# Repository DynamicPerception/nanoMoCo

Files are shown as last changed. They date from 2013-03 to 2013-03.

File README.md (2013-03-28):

nanoMoCo Stepper Controller/Driver
==================================

The nanoMoCo stepper driver/controller is a specialized, Arduino-compatible* device specifically designed to enable advanced multi-axis stepper-based robotics and automation projects less expensive, and easier to create.

This github contains the Eagle files, BOM, and Sketchup files for this board.  To purchase a pre-made board, see http://dynamicperception.com/products/nanomoco-stepper-drivercontroller

Key features of the nanoMoCo include:

- Atmega328P processor running at 16MHz
- 8-16V DC Operation
- Integrated A4983/A4988 bi-polar chopping driver with up to 16x microstepping
     - Up to 800 mA/coil without active cooling
     - Up to 1.5 A/coil with active cooling
- Dual opto-coupled outputs for safe interaction with other devices
- Integrated RS485 bus for multi-node communication over long distances with only two wires
- Leverage the OpenMoCo AVR Libraries and OpenMoCo Qt Libraries to create new software and applications

* requires a special USB to RS485 adapter to use with the Arduino IDE

See http://dynamicperception.com/docs/nanomoco for more information

License and Copyright
---------------------

nanoMoCo is Copyright (c) 2012-2013 Dynamic Perception LLC.

All files shared under the Creative Commons Attibution-Share-Alike 3.0 License.

The nanoMoCo name is a trademark of Dynamic Perception LLC.

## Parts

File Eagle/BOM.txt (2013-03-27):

Part	Value		Device			Sheet	Part #

C1	0.1uF		CAP0402			1	GRM155R71A104KA01D

C10	0.1uF		CAP0402			1	GRM155R71A104KA01D

C2	0.1uF		C-EUC1608		1	CGA3E2X7R1H104K

C3	0.1uF		C-EUC1608		1	CGA3E2X7R1H104K

C4	0.1uF		C-EUC1608		1	CGA3E2X7R1H104K

C7	0.1uF		C-EUC1608		1	CGA3E2X7R1H104K

C5	6pF		CAP0402			1	GRM1555C1H6R0DZ01D

C8	6pF		CAP0402			1	GRM1555C1H6R0DZ01D
C6	0.22uF		C-EUC0805		1	C0805C224K5RACTU

C13	10uF		CAP_POL1206		1	T491A106M020AT

C19	10uF		CAP_POL1206		1	T491A106M020AT

IC1	SN75176A	SN65176D		1	SN75176AD

IC2	A4983		A4983			1	A4983SETTR-T

JP1	COMM		PINHD-2X7		1	not placed

JP2	MOTOR		PINHD-1X4		1	not placed

JP3	ICSP		PINHD-2X3		1	not placed
JP4	ISO		PINHD-1X4		1	not placed

SER	SER		PINHD-2X2		1	not placed

OK1	ACPL-227	ACPL-227		1	ILD207T

OUT1	LED		LEDCHIPLED_0603		1	SML-P12VTT86

PWR	LED		LEDCHIPLED_0603		1	SML-P12VTT86

R1	100K		RESISTOR0402		1	not placed

R8	100K		RESISTOR0402		1	not placed

R2	5.1k		RESISTOR0402		1	RC0402FR-075K1L

R3	5.1k		RESISTOR0402		1	RC0402FR-075K1L

R15	5.1k		RESISTOR0402		1	RC0402FR-075K1L

R4	2.49k		RESISTOR0402		1	RR0510P-2491-D

R5	62		RESISTOR0402		1	CRCW040262R0FKED

R6	10K		RESISTOR0402		1	CRCW040210K0FKEDHP

R7	41.2		RESISTOR0402		1	CRCW040241R2FKED

R9	100		RESISTOR0402		1	not placed

R10	0.01		R-US_R0603		1	ERJ-M03NF10MV

R12	0.01		R-US_R0603		1	ERJ-M03NF10MV

R13	20k		RESISTOR0402		1	ERA-2AEB203X

R14	470		RESISTOR0402		1	RK73B1ETTP471J

R16	470		RESISTOR0402		1	RK73B1ETTP471J

T2	CMPT2369	BCW60-NPN-SOT23-BEC	1	CMPT2369

U$1	CADJ		TC33X-2			1	TC33X-2-103E

U$3	3.2X2.5MMCRYSTAL 3.2X2.5MMCRYSTAL	1	CX3225SB16000D0FLJZZ

U1	ATMEGA328	ATMEGA168		1	ATMEGA328P-AU

U2	MIC5205-5.0YM5	V_REG_LDOSMD		1	MIC5205-5.0YM5 TR

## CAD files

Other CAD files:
Sketchup/nmoco-brd-1t1.skp
Sketchup/nmoco-brd.skp

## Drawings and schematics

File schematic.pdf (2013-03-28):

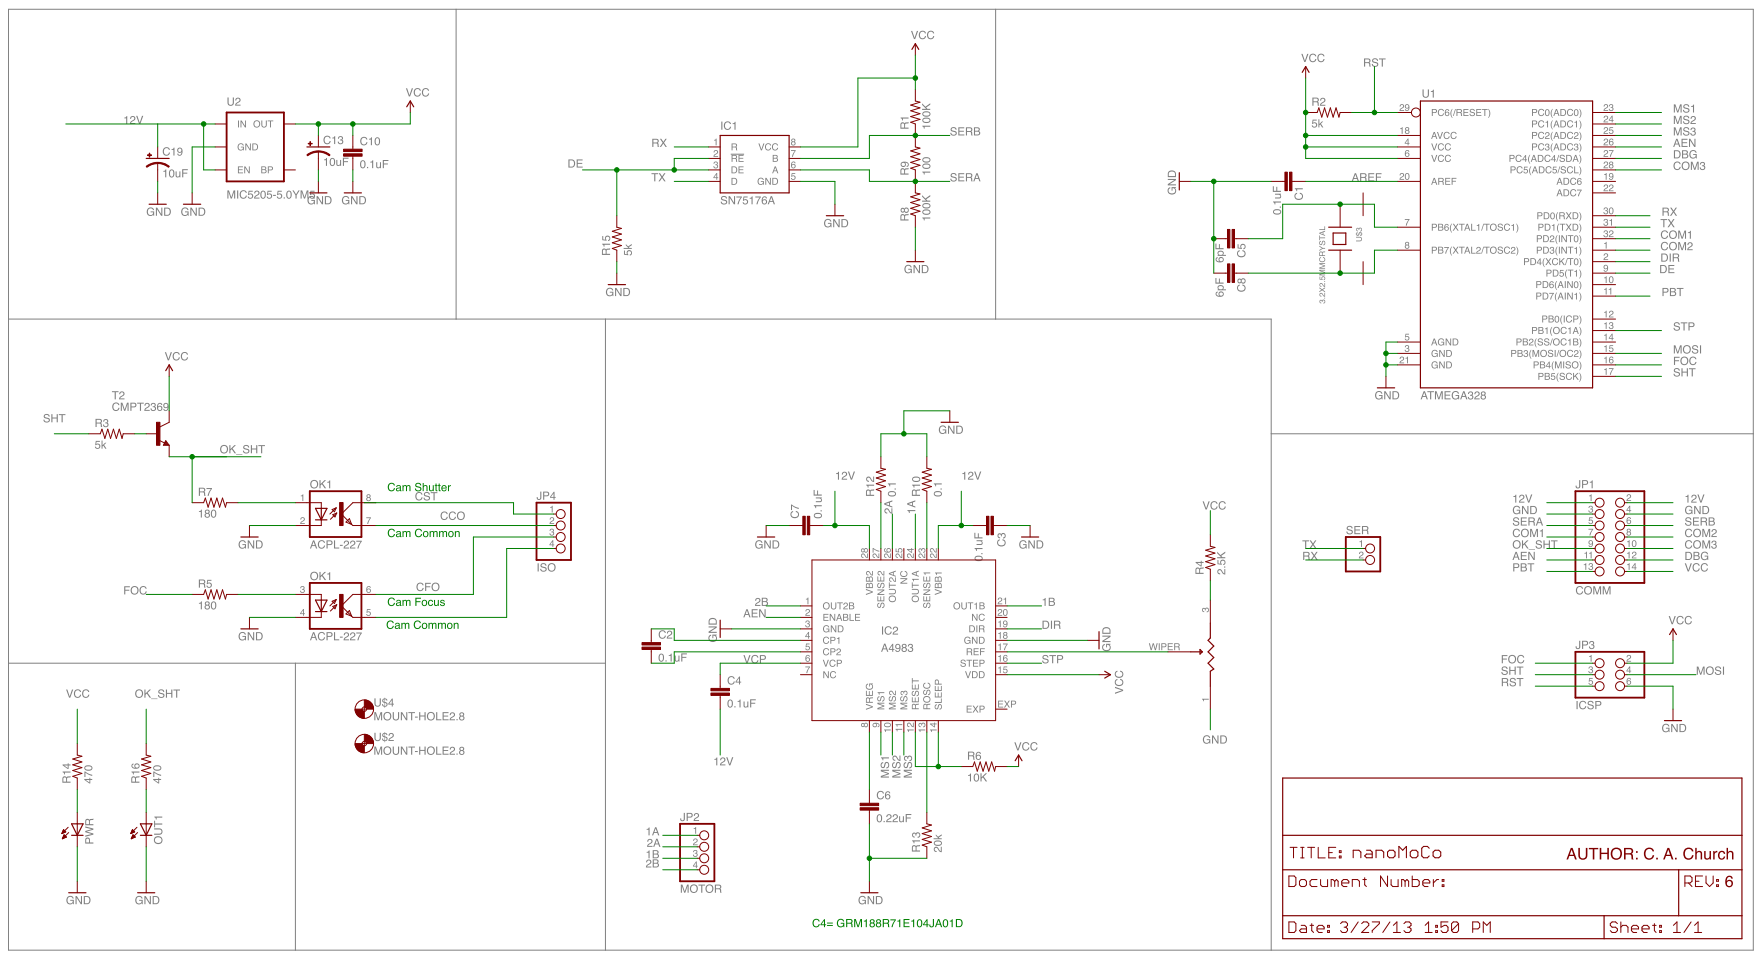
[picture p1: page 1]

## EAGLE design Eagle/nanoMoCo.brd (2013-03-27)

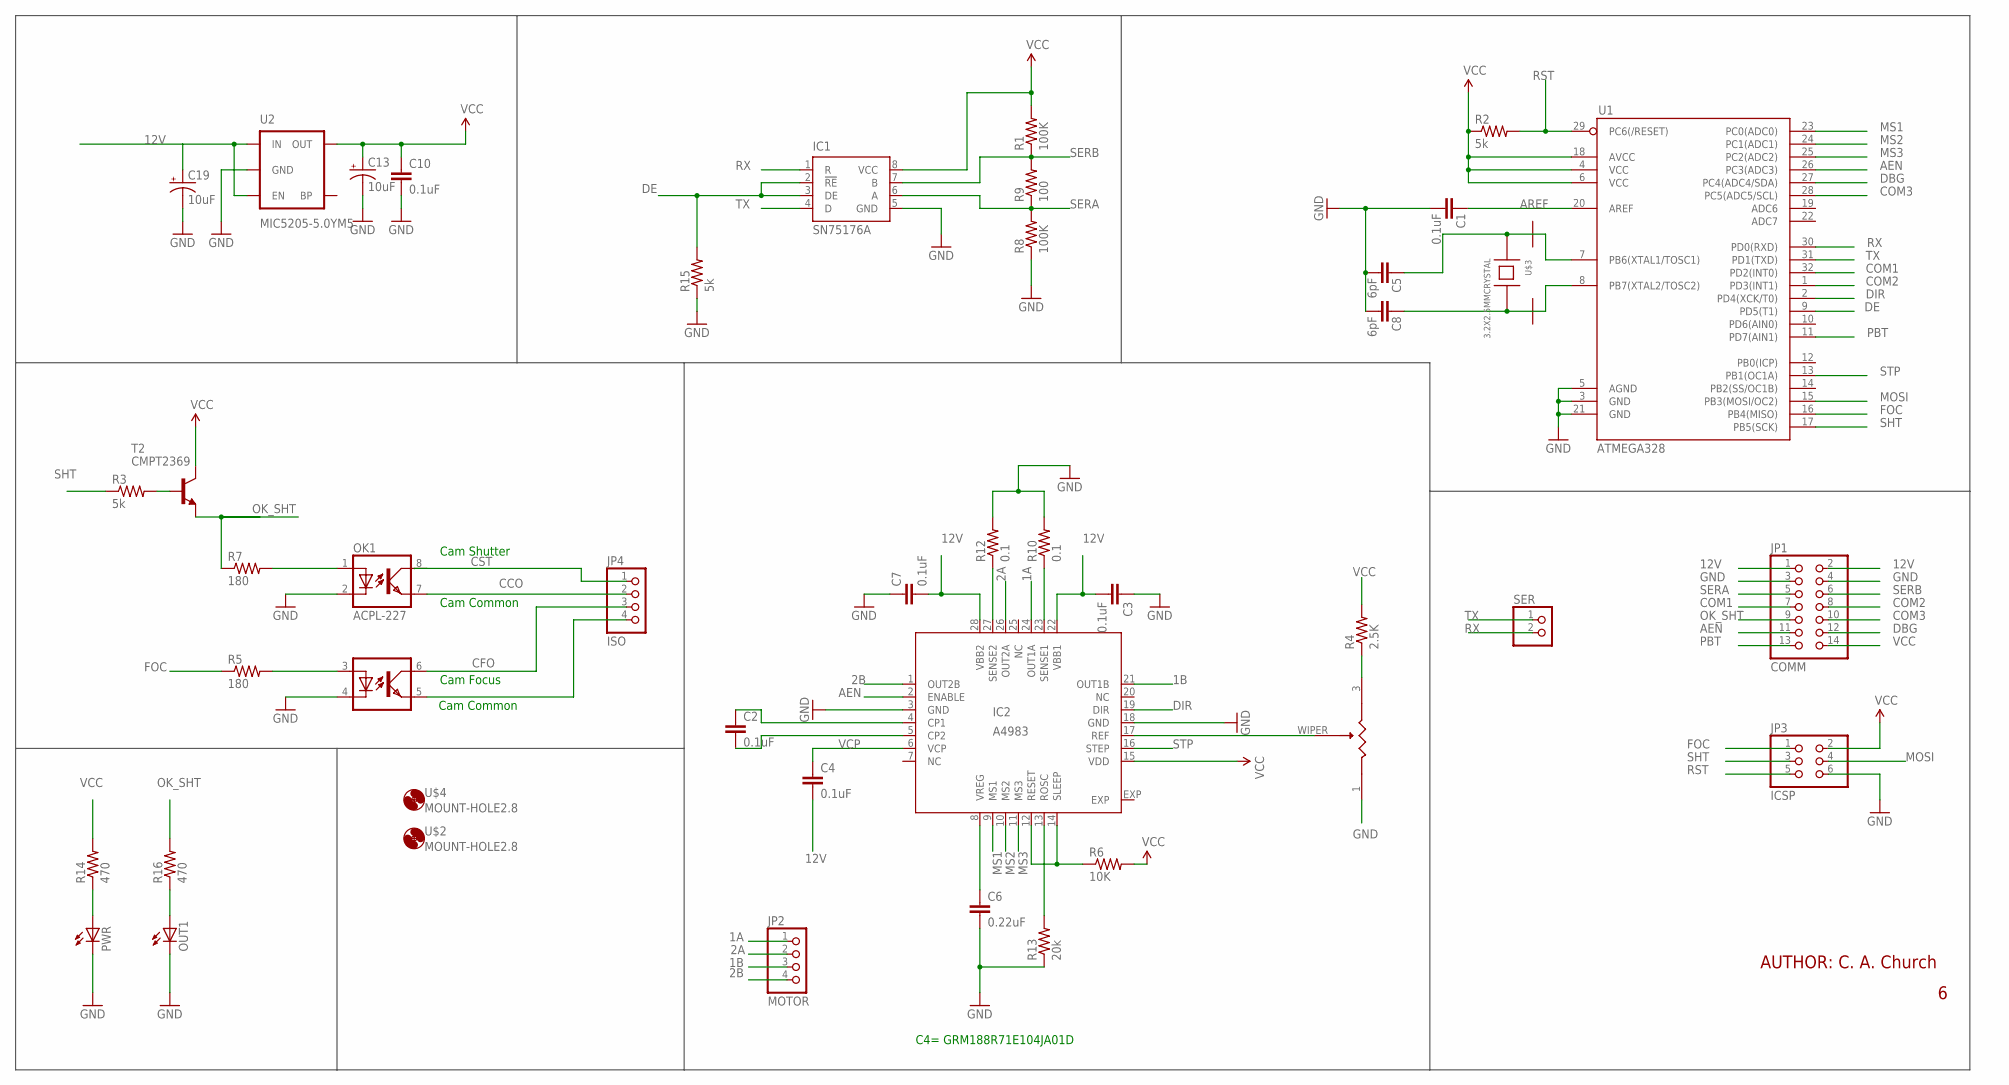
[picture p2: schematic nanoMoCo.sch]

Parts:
C1, C10: 0.1uF; C0402
C2, C3, C4, C7: 0.1uF; C1608
C5, C8: 6pF; C0402
C6: 0.22uF; C0805
C13, C19: 10uF; EIA3216
IC1: SN75176A; SO-08
IC2: A4983; QFN28ET
JP1: COMM; 2X07
JP2: MOTOR; 1X04
JP3: ICSP; 2X03
JP4: ISO; 1X04
OK1: ACPL-227; SOIC8
OUT1: LEDCHIPLED_0603; CHIPLED_0603
PWR: LEDCHIPLED_0603; CHIPLED_0603
R1, R8: 100K; C0402
R2, R3, R15: 5k; C0402
R4: 2.5K; C0402
R5, R7: 180; C0402
R6: 10K; C0402
R9: 100; C0402
R10, R12: 0.1; R0603
R13: 20k; C0402
R14, R16: 470; C0402
SER: PINHD-1X2; 1X02
T2: CMPT2369; SOT23-BEC
U1: ATMEGA328; TQFP32-08
U2: MIC5205-5.0YM5; SOT23-5
U$1: CADJ; 3MMSMD
U$2, U$4: MOUNT-HOLE2.8; 2,8
U$3: 3.2X2.5MMCRYSTAL; 3.2X2.5MM

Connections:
1A: IC2.24 (OUT1A), JP2.1
1B: IC2.21 (OUT1B), JP2.3
2A: IC2.26 (OUT2A), JP2.2
2B: IC2.1 (OUT2B), JP2.4
3.3V: IC1.8 (VCC), R1.2
4: U$3.4
12V: C3.2, C4.2, C7.2, C19.A (+), IC2.22 (VBB1), IC2.28 (VBB2), JP1.1, JP1.2, U2.1 (IN), U2.3 (EN)
AEN: IC2.2 (ENABLE), JP1.11, U1.26 (PC3(ADC3))
AREF: C1.2, U1.20 (AREF)
ARST: IC2.12 (RESET), IC2.14 (SLEEP), R6.1
CCO: JP4.2, OK1.7 (EMIT)
CFO: JP4.3, OK1.6 (COL1)
COM1: JP1.7, U1.32 (PD2(INT0))
COM2: JP1.8, U1.1 (PD3(INT1))
COM3: JP1.10, U1.28 (PC5(ADC5/SCL))
CST: JP4.1, OK1.8 (COL)
DBG: JP1.12, U1.27 (PC4(ADC4/SDA))
DE: IC1.2 (!RE), IC1.3 (DE), R15.2, U1.9 (PD5(T1))
DIR: IC2.19 (DIR), U1.2 (PD4(XCK/T0))
FOC: JP3.1, R5.1, U1.16 (PB4(MISO))
GND: C1.1, C3.1, C5.1, C6.2, C7.1, C8.1, C10.2, C13.C (-), C19.C (-), IC1.5 (GND), IC2.3 (GND), IC2.18 (GND), JP1.3, JP1.4, JP3.6, OK1.2 (C), OK1.4 (C1), OUT1.C, PWR.C, R8.1, R10.2, R12.2, R13.1, R15.1, U1.3 (GND), U1.5 (AGND), U1.21 (GND), U2.2 (GND), U$1.1, U$3.2 (GND)
MOSI: JP3.4, U1.15 (PB3(MOSI/OC2))
MS1: IC2.9 (MS1), U1.23 (PC0(ADC0))
MS2: IC2.10 (MS2), U1.24 (PC1(ADC1))
MS3: IC2.11 (MS3), U1.25 (PC2(ADC2))
unnamed: R4.1, U$1.3
unnamed: PWR.A, R14.1
unnamed: OUT1.A, R16.1
unnamed: C2.1, IC2.4 (CP1)
unnamed: C2.2, IC2.5 (CP2)
unnamed: JP4.4, OK1.5 (EMIT1)
unnamed: OK1.1 (A), R7.2
unnamed: OK1.3 (A1), R5.2
unnamed: IC2.17 (REF), U$1.WIPER (2)
unnamed: IC2.23 (SENSE1), R10.1
unnamed: IC2.27 (SENSE2), R12.1
unnamed: R3.2, T2.B
OK_SHT: JP1.9, R7.1, R16.2, T2.E
PBT: JP1.13, U1.11 (PD7(AIN1))
ROSC: IC2.13 (ROSC), R13.2
RST: JP3.5, R2.2, U1.29 (PC6(/RESET))
RX: IC1.1 (R), SER.2, U1.30 (PD0(RXD))
SERA: IC1.6 (A), JP1.5, R8.2, R9.1
SERB: IC1.7 (B), JP1.6, R1.1, R9.2
SHT: JP3.3, R3.1, U1.17 (PB5(SCK))
STP: IC2.16 (STEP), U1.13 (PB1(OC1A))
TX: IC1.4 (D), SER.1, U1.31 (PD1(TXD))
VCC: C10.1, C13.A (+), IC2.15 (VDD), JP1.14, JP3.2, R2.1, R4.2, R6.2, R14.2, T2.C, U1.4 (VCC), U1.6 (VCC), U1.18 (AVCC), U2.5 (OUT)
VCP: C4.1, IC2.6 (VCP)
VREG: C6.1, IC2.8 (VREG)
XTAL1: C5.2, U1.7 (PB6(XTAL1/TOSC1)), U$3.1
XTAL2: C8.2, U1.8 (PB7(XTAL2/TOSC2)), U$3.3

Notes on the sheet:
Cam Shutter
Cam Common
Cam Focus
C4= GRM188R71E104JA01D
AUTHOR: C. A. Church

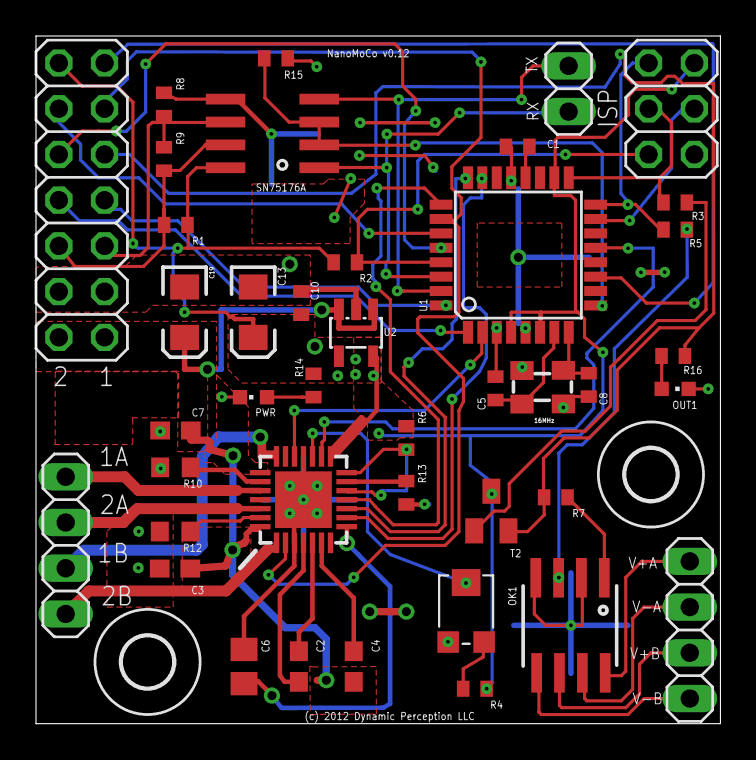
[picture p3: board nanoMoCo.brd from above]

Board: 2 copper layers, 38.0 x 38.2 mm, 43 parts (0 on the bottom side), 51 nets.

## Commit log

2013-03-27 * Added required files
    [nanoMoCo.brd, nanoMoCo.sch, nmoco-brd-1t1.skp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]
2013-03-28 * Added Schematic PDF

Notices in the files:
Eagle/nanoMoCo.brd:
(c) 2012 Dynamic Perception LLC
